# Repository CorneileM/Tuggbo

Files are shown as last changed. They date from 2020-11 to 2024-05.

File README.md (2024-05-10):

# Tuggbo
## Type: Robot/Thingy
### An automated filament pulling device to control 3D-printer filament diameter when exiting a filament extruder

This repository contains circuit diagrams, 3D-printed parts, and Arduino sketches for a filament pulling device designed to control the diameter of 3D-printer filament exiting a desktop extruder (in this case, a Filabot EX2).

The diameter of the filament is controlled by the speed of a DC motor which pulls filament from an extruder:
faster pulling = thinner filament; slower pulling = thicker filament. The filament is air- or water-cooled before it reaches the filament pulling machine. The speed of the DC motor is adjusted based on the measured filament diameter
which is read from a Mitutoyo digital plunge-dial indicator, to obtain a stable filament diameter. Because there's a lag period between filament exiting the extruder and being measured and an additional lag period between Tuggbo pulling speed adjustments and filament diameter change, I implemented a PID controller algorithm to obtain a stable filament diameter. 

The repository also includes an Arduino sketch and circuit diagram for a PID controlled heater that is placed inside the FILABOT EX2 hopper, to pre-heat and soften plastic pellets 
before entering the extrusion screw. This functions to prevent the the extrusion screw from being blocked by large pieces of hard plastic. This is specific to my application of producing filament from recycled plastic bottles. Preheating allowed for smoother plastic flow from the hopper into the extruder screw.

<br>

#### Tuggbo

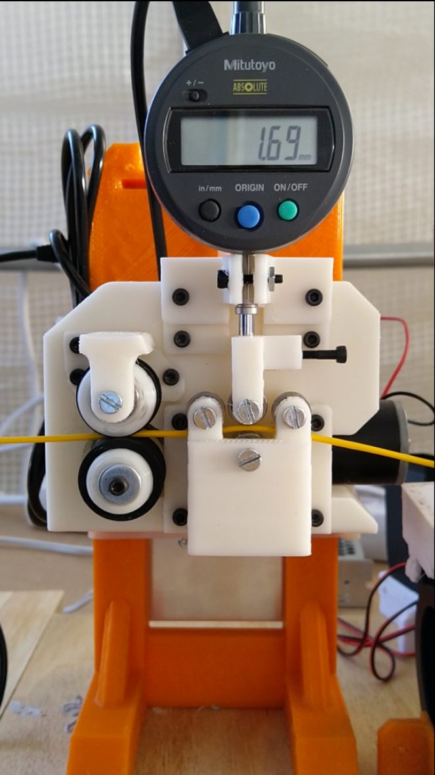
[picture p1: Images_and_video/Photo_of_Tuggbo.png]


<br>

### Useful resources and background information
#### PID process control
[Interfacing a digital micrometer and a microcontroller]( https://www.instructables.com/id/Interfacing-a-Digital-Micrometer-to-a-Microcontrol/ )

[Arduino PID library](https://playground.arduino.cc/Code/PIDLibrary/)

[PID explained for process engineers](https://www.aiche.org/resources/publications/cep/2016/february/pid-explained-process-engineers-part-2-tuning-coefficients)

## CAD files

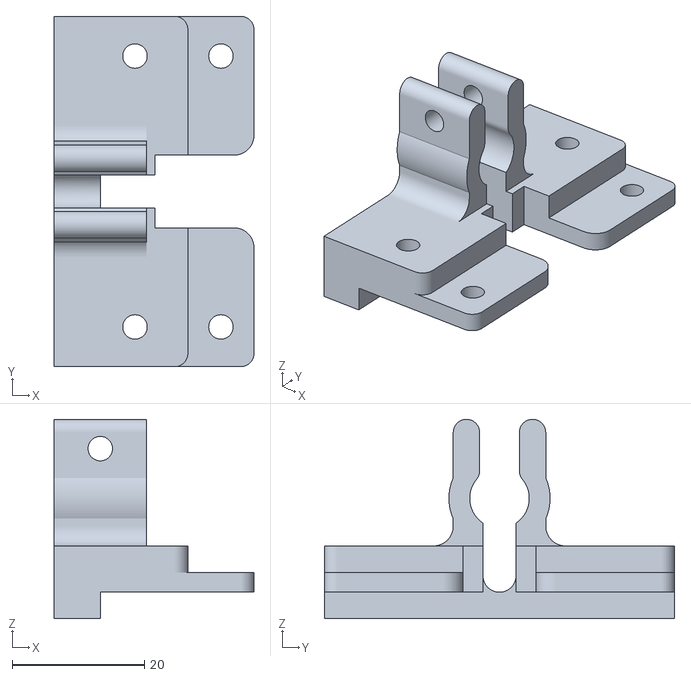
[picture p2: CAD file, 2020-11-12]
Tuggbo_3D_printed_parts/STLs/MituBaseClamp.stl
30.2 x 53.0 x 30.1

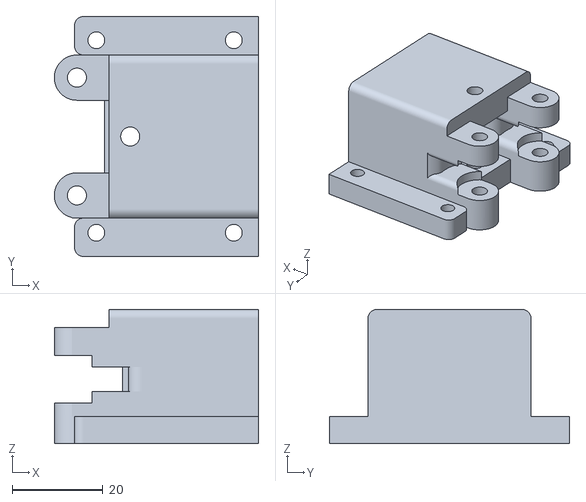
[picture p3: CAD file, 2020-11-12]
Tuggbo_3D_printed_parts/STLs/MituGhousing.stl
45.1 x 53.0 x 29.6

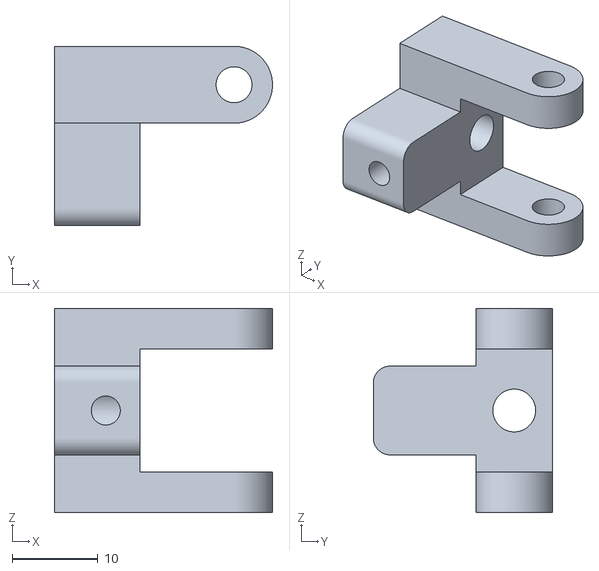
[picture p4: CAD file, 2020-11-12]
Tuggbo_3D_printed_parts/STLs/MituTip.stl
25.5 x 21.0 x 23.9

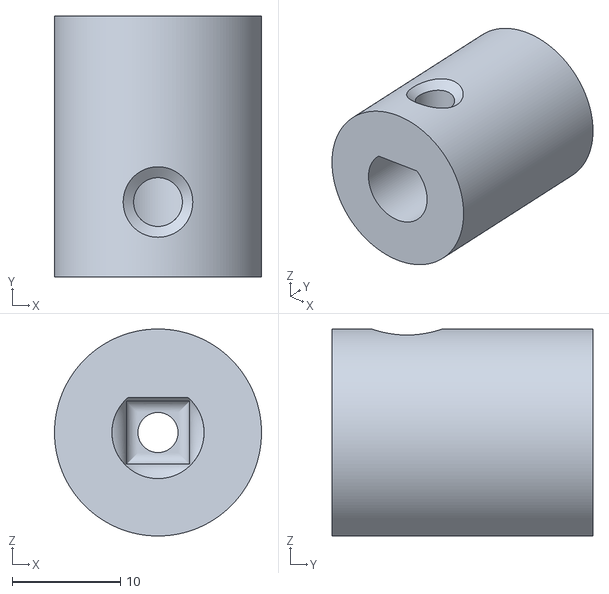
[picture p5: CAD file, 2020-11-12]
Tuggbo_3D_printed_parts/STLs/RWmotShaftIn.stl
19.1 x 24.0 x 19.1

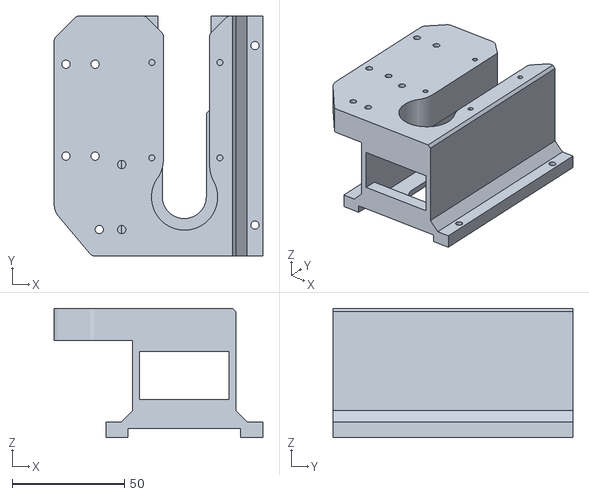
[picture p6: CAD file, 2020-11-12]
Tuggbo_3D_printed_parts/STLs/EngineCarriage.stl
93.0 x 107.0 x 57.6

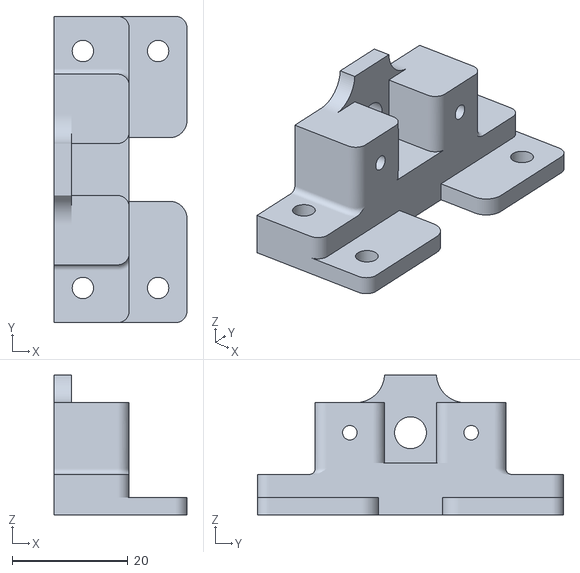
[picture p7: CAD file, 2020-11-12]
Tuggbo_3D_printed_parts/STLs/PullTensBase.stl
23.0 x 53.0 x 24.1

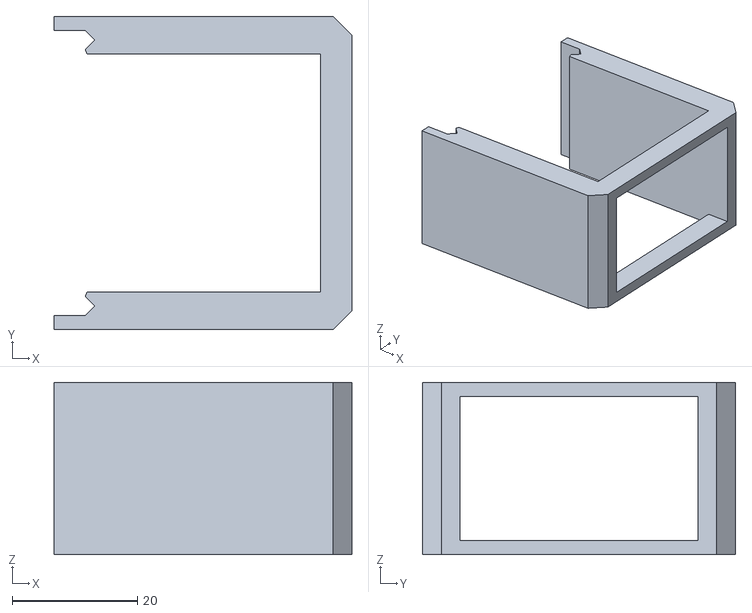
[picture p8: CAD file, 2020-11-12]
Tuggbo_3D_printed_parts/STLs/FanTop.stl
47.5 x 50.0 x 27.5

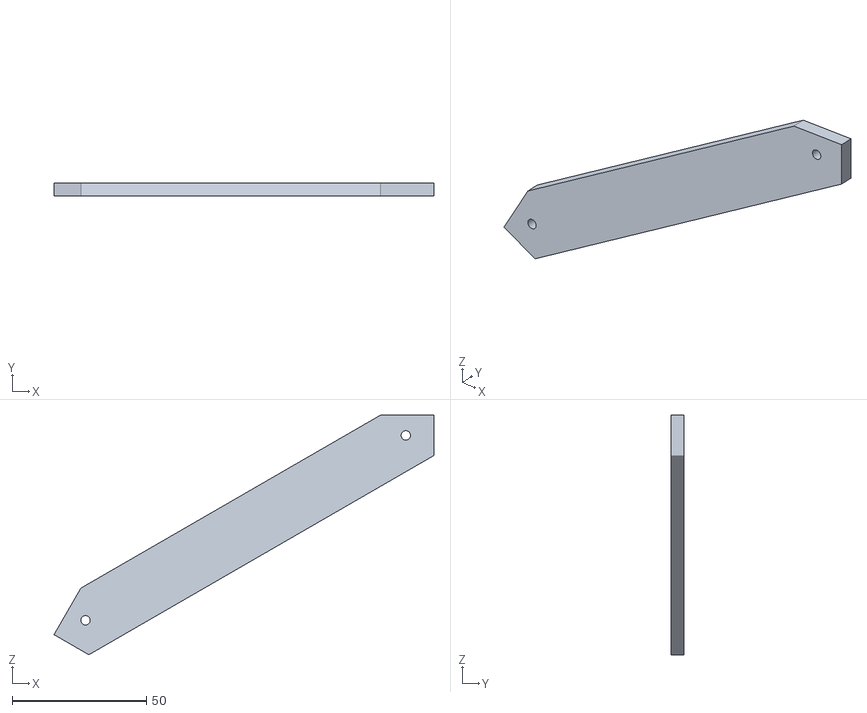
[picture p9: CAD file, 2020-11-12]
Tuggbo_3D_printed_parts/STLs/FanStruts.stl
141.6 x 5.00 x 89.3

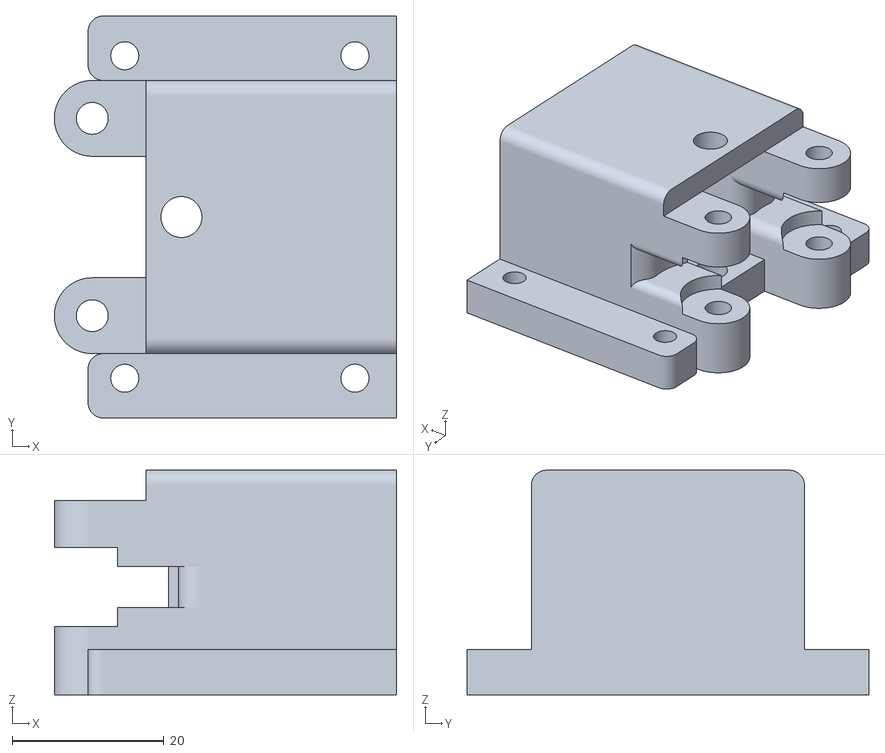
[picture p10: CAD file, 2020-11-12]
Tuggbo_3D_printed_parts/STLs/MotorGhousing.stl
45.1 x 53.0 x 29.6

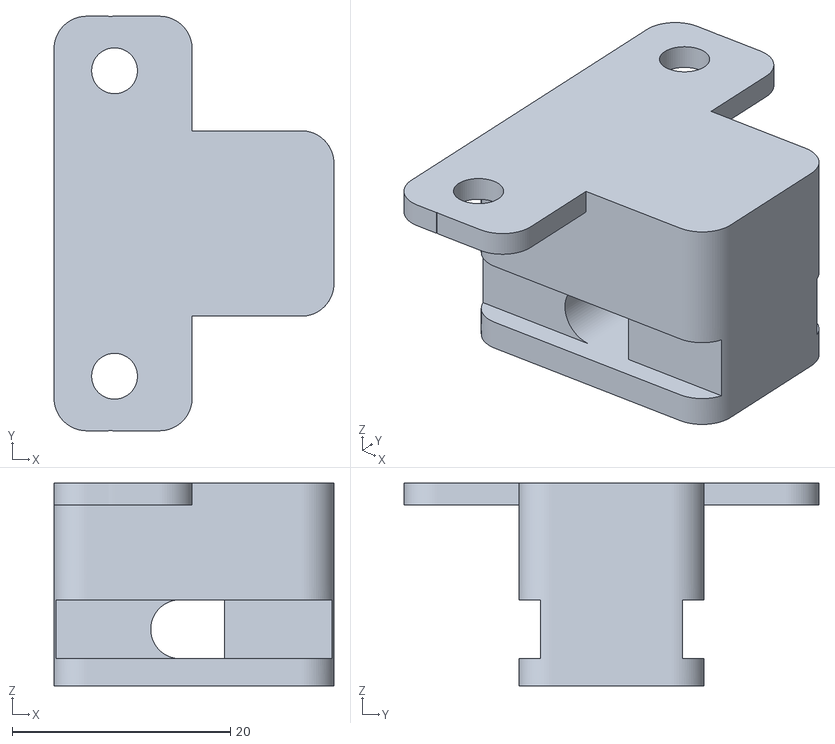
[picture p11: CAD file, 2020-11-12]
Tuggbo_3D_printed_parts/STLs/FillConduit.stl
25.7 x 38.0 x 18.6

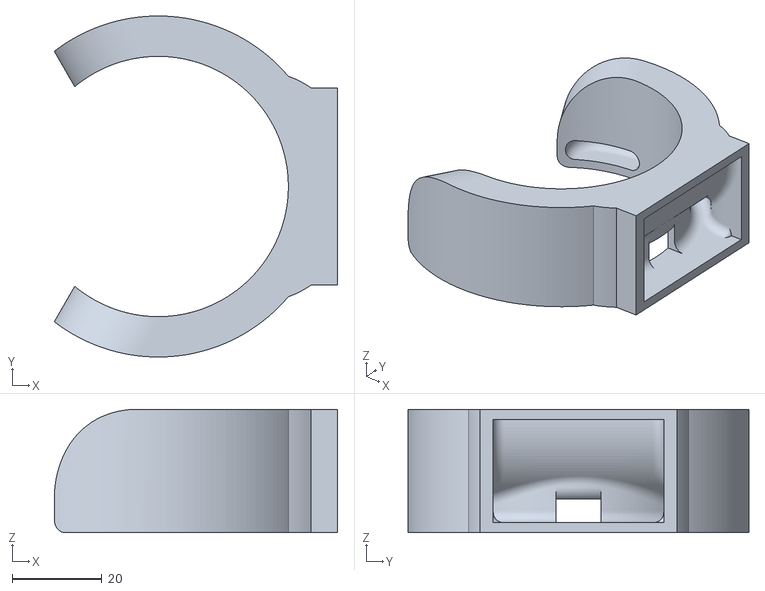
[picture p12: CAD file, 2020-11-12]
Tuggbo_3D_printed_parts/STLs/FanJets.stl
63.2 x 76.0 x 27.5

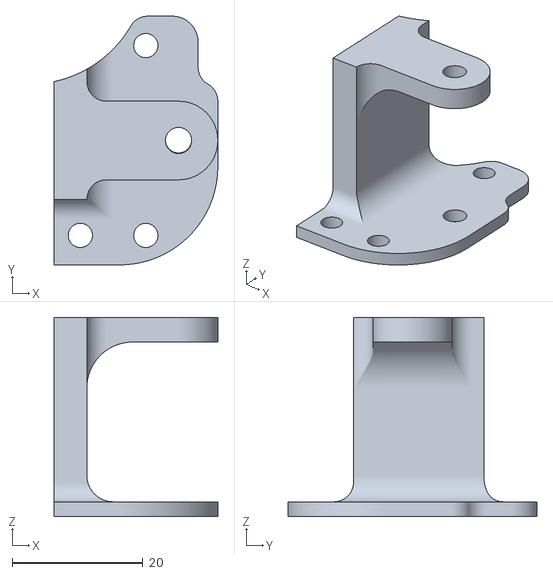
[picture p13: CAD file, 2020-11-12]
Tuggbo_3D_printed_parts/STLs/FreeWheelSupp.stl
25.0 x 38.0 x 30.4

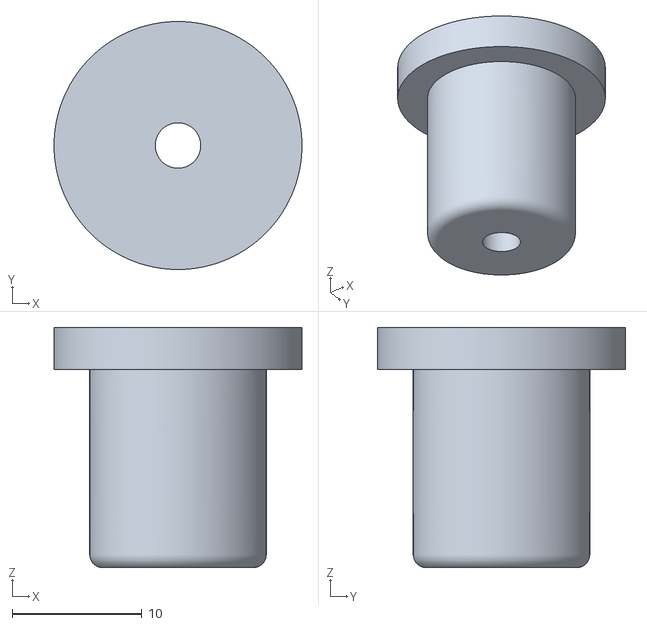
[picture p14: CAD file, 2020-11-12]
Tuggbo_3D_printed_parts/STLs/RWmotShaftOut.stl
19.1 x 19.1 x 18.5

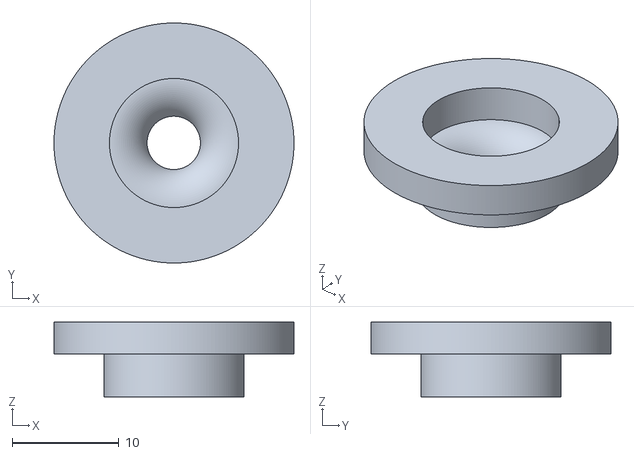
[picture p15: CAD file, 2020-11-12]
Tuggbo_3D_printed_parts/STLs/FreeWheelAxle.stl
22.5 x 22.5 x 7.00

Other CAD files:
Tuggbo_3D_printed_parts/STLs/PullTensPist.stl
Tuggbo_3D_printed_parts/STLs/FanBase.stl
Tuggbo_3D_printed_parts/STLs/FanBaseFilabot.stl

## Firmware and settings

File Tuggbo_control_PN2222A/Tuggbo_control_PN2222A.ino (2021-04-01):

//This sketch governs the behaviour of a filament pulling device designed to control the diameter of filament.
//The diameter of the filament is controlled by the speed of a DC motor which pulls filament from an extruder (Filabot EX2): faster = thinner filament; slower = thicker filament.
//The speed of the DC motor is adjusted based on the measured filament diameter which is read from a Mitutoyo digital plunge-dial indicator, to obtain a stable filament diameter.

//This sketch incoporates code from SSpence for reading data from the Mitutoyo plangue dial: https://www.instructables.com/id/Interfacing-a-Digital-Micrometer-to-a-Microcontrol/ 

  
//**LIBRARIES**//
#include <PID_v1.h>
#include <MovingAverage.h>

//**PIN AND VARIABLE DECLARATIONS**//

  //*MITUTOYO*//
    const int req = 5; //Mitutoyo REQ line goes to pin 5 through q1 (arduino high pulls request line low)
    const int dat = 2; //Mitutoyo Data line goes to pin 2
    const int clk = 3; //Mitutoyo Clock line goes to pin 3


   //Mitutoyo data variables//
    int i = 0;
    int j = 0;
    int k = 0;
    float MITread_x;
    float MITreadPush;
    float MITreadAve;
    float MITreadAveDiff;
    //const float MIToffset = 30; //Tuggbo#1
    //const float MIToffset = 20; //Tuggbo#2
    const float MIToffset = 15; //Tuggbo#3
                              //Because of a slight groove in the Mitutoyo's filament guide bearing, there is a 0.3 mm offset -- we multiply the offset by 100 to correspond with the raw data from the Mitutoyo
                              //The offset is currently subtracted manually and directly from setpoint and measured values, but will be implemented automatically at a later stage to give more intuitive outputs
    const float FilamentDiam = 1.65; //Sets the filament diameter goal we want. Units are mm/100. At the moment we're aiming for 1.35 mm filament
                                  //this seems to be the best diameter to achieve sufficient cooling with the current setup.

    float TargetHIGH = FilamentDiam+0.16;
    float TargetLOW = FilamentDiam-0.16;
    
    byte mydata[14];
    String value_str;
    long value_int;
    float value;
  
  //*MOSFET MOTOR CONTROLLER*//
    const int MOSFET = 6; //MOSFET PID (PWM) output goes through pin 6 -- this needs to be a PWN pin. On the Nano Every that's D3, D5, D6, D9, D10
    int pwmStart = 70; //variable determining motor speed
                       //stable at 55 

  //*PID FILAMENT DIAMETER CONTROL*//
    //define PID Variables
    double Setpoint, Input, Output;
    float Kp = 2; //The proportional gain (Kp) determines the ratio of output response to the error signal. In general, increasing the proportional gain will increase the speed of the control system response
                  //I'm setting this to 0.3, since preliminary tests showed that Tuggbo was reacting too quickly, even at Kp = 2
                  //0.5
                  
    float Ki = 0.75; //The integral component sums the error term over time. The result is that even a small error term will cause the integral component to increase slowly.
                    //The integral response will continually increase over time unless the error is zero, so the effect is to drive the Steady-State error to zero.
                    //0.15
                    
    float Kd = 0.25; //The derivative component causes the output to decrease if the process variable is increasing rapidly (in our case, this is reversed).
                  //The derivative response is proportional to the rate of change of the process variable.
                  //Increasing the derivative time (Td) parameter will cause the control system to react more strongly to changes in the error term and will increase the speed of the overall control system response.
                  //Most practical control systems use very small derivative time (Td), because the Derivative Response is highly sensitive to noise in the process variable signal.
                  //0.2
    
    //Specify the links and initial tuning parameters
    PID tuggboPID(&Input, &Output, &Setpoint, Kp, Ki, Kd, P_ON_E, REVERSE); //PID coefficients were taken from http://electronoobs.com/eng_arduino_tut24_2.php as a starting poinoinoi
                                                                      //I used to have the PID run on P_ON_M mode (proportional on measurement), but this seemed to make the PID very "scared" of going too close to the setpoint
                                                                      //Overshoot is not a big deal in this application, so I've switched this back to the standard proportional on error mode (P_ON_E)
                                                                      //We specify REVERSE, since the thicker the filament gets, the higher the output needs to be
  
  //*MOVING AVERAGE VARIABLES*//
    //Sets up the movingAverage function with 50 readings (1 per millisecond) per moving average window with a starting value of 0
    //This function will constantly calcualte a moving average for smoothed Mitutoyo readings -- the moving average window also serves to moderate Tuggbo's control response to make it less jerky 
    MovingAverage<float> MITread(5, 0);

    // Generates the first input for the MovingAverage function
    //float MITread_x = FilamentDiam*100;

    
void setup() {
  
  Serial.begin(9600); //Start serial communication

  //*MITUTOYO*//
    pinMode(req, OUTPUT); //Set the req (5) pin as an output so that data requests can be triggered by setting the pin LOW
    pinMode(clk, INPUT_PULLUP); //To obtain data we will read from the clk and dat pins, so they need to be set to INPUT with internal PULLUP resistors to stop noisy readings
    pinMode(dat, INPUT_PULLUP); //To obtain data we will read from the clk and dat pins, so they need to be set to INPUT with internal PULLUP resistors to stop noisy readings
    digitalWrite(req, LOW); // set initial state of req (5) pin to HIGH so that data can be requested from Mitutoyo by setting the pin LOW

  //*MOSFET MOTOR CONTROLLER*//
    //MOSFET pin is set to output so that we can send PWM signals to control the motor
    pinMode(MOSFET, OUTPUT); 

    //Define Input and Setpoint and turn the PID on
    Input = MITreadAve*100;
    Setpoint = FilamentDiam*100;
    tuggboPID.SetOutputLimits(pwmStart, 250); //since the motor only starts working at 43 PWM, we need to set the PWM min to 43. 70 is plenty fast, so I'm capping the max here.
    tuggboPID.SetMode(AUTOMATIC);

    //Starts the motor in forward direction at the motor starting speed
    analogWrite(MOSFET, pwmStart);
  
}

void loop() {

 //*MITUTOYO*//
   //get readings from the SPC cable (see https://www.instructables.com/id/Interfacing-a-Digital-Micrometer-to-a-Microcontrol/ for details)
  
    digitalWrite(req, HIGH); // request data from Mitutoyo

    for( i = 0; i < 13; i++ ) {
      k = 0;
      for (j = 0; j < 4; j++) {
        while( digitalRead(clk) == LOW) {
          } // hold until clock is high
          while( digitalRead(clk) == HIGH) {
            } // hold until clock is low
            bitWrite(k, j, (digitalRead(dat) & 0x1));
        }
        mydata[i] = k;
      }
    
    // assemble measurement from bytes    
    
    char buf[7];
    for(int lp=0;lp<6;lp++)
    buf[lp]=mydata[lp+5]+'0';
    buf[6]=0;
    MITread_x = atol(buf); //assembled measurement, no decimal place added
   
    digitalWrite(req, LOW); //reset req (5) pin to HIGH to stop data request
    
  //*MOVING AVERAGE CALCULATION*//
    // Pushes the MITUTOYO reading as an input to the moving average object
    /*if(MITread_x > 180){ // outliers sometimes pop up and cause shit... this eliminates false highs
      MITread_x = 180;
      
    }if(MITread_x < 60){ // outliers sometimes pop up and cause shit... this eliminates false lows
      MITread_x = 60;
    }*/

    MITreadPush = (MITread_x + MIToffset)/100;
    if(MITread.size() > 4){
      MITreadAveDiff = abs(MITreadPush - MITread.get());
      if(MITreadAveDiff > 0.25){
         delay(10);
         //get readings from the SPC cable (see https://www.instructables.com/id/Interfacing-a-Digital-Micrometer-to-a-Microcontrol/ for details)
  
            digitalWrite(req, HIGH); // request data from Mitutoyo
        
            for( i = 0; i < 13; i++ ) {
              k = 0;
              for (j = 0; j < 4; j++) {
                while( digitalRead(clk) == LOW) {
                  } // hold until clock is high
                  while( digitalRead(clk) == HIGH) {
                    } // hold until clock is low
                    bitWrite(k, j, (digitalRead(dat) & 0x1));
                }
                mydata[i] = k;
              }
            
            // assemble measurement from bytes    
            
            char buf[7];
            for(int lp=0;lp<6;lp++)
            buf[lp]=mydata[lp+5]+'0';
            buf[6]=0;
            MITread_x = atol(buf); //assembled measurement, no decimal place added
           
            digitalWrite(req, LOW); //reset req (5) pin to HIGH to stop data request

            MITreadPush = (MITread_x + MIToffset)/100;
            MITread.push(MITreadPush);
            
      } else {
        MITread.push(MITreadPush);
      }
    } else {
      MITread.push(MITreadPush);
    }

    // Prints each value stored in the moving average for debugging
    for (uint8_t i = 0; i < MITread.size(); i++) {
      Serial.print(MITread[i]);
      Serial.print(" ");
    }  

    MITreadAve = MITread.get();
    //Prints the moving average
    Serial.print(" = | ");
    Serial.print(MITread.get());
    Serial.print(" mm |");
    
    //*PID FILAMENT DIAMETER CONTROL*//
    //if there is no filament is present, we want the motor to continue turning at its minimum speed (0.2 mm is a safe margin for no filament being present)
    //if filament has been fed in (i.e., the Mitutoyo reads higher than 0.2) start PID motor control  
    if(MITreadAve < 1.00) { 
       Serial.print("   THIN/NO FILAMENT: "); //for debugging purposes
       Serial.println(pwmStart); //for debugging purpose
       
       analogWrite(MOSFET, pwmStart); 
    } else {
      Input = MITreadAve*100;
      Setpoint = FilamentDiam*100;
      tuggboPID.Compute();
      analogWrite(MOSFET, Output);
      
      if(MITreadAve > TargetLOW && MITreadAve < TargetHIGH) { 
        Serial.print("   TARGET: "); //for debugging purposes
        Serial.println(Output); //for debugging purposes+
        }
        
      if(MITreadAve > TargetHIGH) {       
        Serial.print("   THICK: "); //for debugging purposes
        Serial.println(Output); //for debugging purposes
        }

      if(MITreadAve < TargetLOW) {
        Serial.print("   THIN: "); //for debugging purposes
        Serial.println(Output); //for debugging purposes
      }
    }
    
delay(200);

}

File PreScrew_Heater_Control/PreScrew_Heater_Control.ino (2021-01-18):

// This Arduino sketch reads the voltage across a NTC (negative-temperature coefficient) thermistor, converts it to a temperature reading
// and switches a MOSFET connected to a heater cartridge on and of through a PWM signal to keep the temperature close to a set point which is controlled by a rotary encoder.
// Both the set point temperature and actual temperature are displayed on a LCD screen

//**CODE SOURCES**//
// Thermistor reading code, including calibration coefficients for the thermistor were taken from a blog post by Joshua Hrisko: https://makersportal.com/blog/2019/1/15/arduino-thermistor-theory-calibration-and-experiment
// Rotary encoder interrupt code for Arduino Nano every adapted from forum discussion: https://forum.arduino.cc/index.php?topic=694732.0 

//**PIN OUTS**//

  /*ARDUINO -> LCD
   *A4 -> SDA
   *A5 -> SCL
   *5V -> LCD_5V
   *GND -> LCD_GND (make sure LCD ground is separate from the rest of the grounds)
   */
  
  /*ARDUINO -> ROTARY ENCODER
   *D2 -> A
   *D3 -> B
   *5V -> VCC
   *GND -> GND
   */
  
  /*ARDUINO -> THERMISTOR
   * A0 -> THERMISTOR LEAD 1 (one of the Thermistor leads, doesn't matter which one)
   * GND -> THERMISTOR LEAD 2 (one of the Thermistor leads, doesn't matter which one)
   * 3.3V -> Resistor (220K ohm) -> THERMISTOR LEAD 1 
   * There's also a 10uF capacitor connected between GND and 3.3V of the Arduino to reduce noise in the thermistor signal
   */
  
  /*ARDUINO -> MOSFET
   * 
   */

//**LIBRARIES**//
#include <Wire.h>
#include <LiquidCrystal_I2C.h>
#include <math.h>
#include <PID_v1.h>
#include <thermistor.h>

//**PIN AND VARIABLE DECLARATIONS**//

  //*LCD*//
    LiquidCrystal_I2C lcd(0x27,2,1,0,4,5,6,7);  // set the LCD address to 0x27 for a 16 chars and 2 line display

  //*ROTARY ENCODER*//
    static int pinA = 2; // Our first hardware interrupt pin is digital pin 2
    static int pinB = 3; // Our second hardware interrupt pin is digital pin 3
    volatile byte aFlag = 0; // let's us know when we're expecting a rising edge on pinA to signal that the encoder has arrived at a detent
    volatile byte bFlag = 0; // let's us know when we're expecting a rising edge on pinB to signal that the encoder has arrived at a detent (opposite direction to when aFlag is set)
    volatile int encoderPos = 30; //this variable stores our current value of encoder position. Change to int or uin16_t instead of byte if you want to record a larger range than 0-255
    volatile int oldEncPos = 0; //stores the last encoder position value so we can compare to the current reading and see if it has changed (so we know when to print to the serial monitor)
    volatile byte reading = 0; //somewhere to store the direct values we read from our interrupt pins before checking to see if we have moved a whole detent

  //*THERMISTOR*//
    thermistor therm1(A0,80);  // Analog Pin which is connected to the 3950 thermistor 100K connected to a 4k7 Pull up and 10Uf Capacitor. 80 represents the configuration in the library for this thermistor
    float T_conv;
    float THERMconvRead;

  //*PID TEMPERATURE CONTROL*//
    //define PID Variables
    double Setpoint, Input, Output;
  
    //Specify the links and initial tuning parameters
    PID heaterPID(&Input, &Output, &Setpoint,9.1,0.3,1.8,P_ON_M, DIRECT); //PID coefficients were taken from http://electronoobs.com/eng_arduino_tut24_2.php as a starting poinoinoi
                                                                      //P_ON_M specifies that Proportional on Measurement be used (see: http://brettbeauregard.com/blog/2017/06/introducing-proportional-on-measurement/)
                                                                      //We also specify DIRECT, since the hotter the cartridge gets, the lower the output needs to be
                                                                      
  //*MOSFET heater switch*//
    const int MOSFET = 6; //MOSFET PID (PWM) output goes through pin 6 -- this needs to be a PWN pin. On the Nano Every that's D3, D5, D6, D9, D10

  //*TIMING VARIABLES*//
    //We'll use millis as a timer to loop through multiple samplings of the thermistor, and a samplecounter to set and keep track of the number of samples taken before averaging the reads
    unsigned long previousMillis = 0; //set to zero to begin
    const int intervalMillis = 100; //sets the sampling interval that we want -- let's set the interval to 0.2 seconds for now
    unsigned int sampleCount = 0; //placeholder to count the number of sample readings taken from the Thermistor
    const byte sampleNum = 10; //sets the number of samples we want to take before averaging-- let's set this to 10 for now, which gives us an average reading over 2 seconds
    unsigned int THERMreadTotal = 0; //placeholder to add each new reading to. This will be divided by sampleNum once sampleNum is reached to get an average

void setup() {

  //setup pins and interrupts for rotary encoder
  pinMode(pinA, INPUT_PULLUP); // set pinA as an input, pulled HIGH to the logic voltage (5V or 3.3V for most cases)
  pinMode(pinB, INPUT_PULLUP); // set pinB as an input, pulled HIGH to the logic voltage (5V or 3.3V for most cases)
  attachInterrupt(digitalPinToInterrupt(pinA), PinA, RISING); // set an interrupt on PinA, looking for a rising edge signal and executing the "PinA" Interrupt Service Routine (below)
  attachInterrupt(digitalPinToInterrupt(pinB), PinB, RISING); // set an interrupt on PinB, looking for a rising edge signal and executing the "PinB" Interrupt Service Routine (below)

  //initialize serial communication at 9600 bits per second:
  Serial.begin(9600);

  //Define Input and Setpoint and turn the PID on
  Input = T_conv;
  Setpoint = encoderPos;
  heaterPID.SetMode(AUTOMATIC);

  //set analog reference to read AREF pin
  analogReference(EXTERNAL);

  //setup LCD  
  lcd.begin(16,2); // initialize the lcd 
  lcd.setBacklightPin(3,POSITIVE);
  lcd.setBacklight(HIGH);
  lcd.clear();
  lcd.setCursor(0,0);  
  lcd.print("T:      Tset:"); // print prepeositions of temperature and Tset on LCD 
  lcd.setCursor(0,1);  
  lcd.print("Output:   "); // print prepeositions of temperature and Tset on LCD 

  // Display default Tset
  lcd.setCursor(13,0);
  lcd.print(encoderPos);   
    
}

//**ROTARY ENCODER INTERRUPT CODE**//
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

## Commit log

2020-11-12 Added 3D printed part STL files and gcode
    [EngineCarriage.stl, FanBase.stl, FanBaseFilabot.stl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]
2020-11-13 Changed description of motor controller to MOSFET motor controller
2020-11-17 Changed motor speed control to Proportional-Integral-Derivative (PID) control.
    The simple proportional control loop I wrote before was resulting in very choppy motor speed adjustments. I'm hoping that implementing PID motor speed control will smooth things out a bit.
2020-12-03 Put the PID control function inside of the averaging loop for filament diameter
    This presumably results in better syncing between the PID control function and filament measurements.
2020-12-03 Update Filament_puller_control.ino
    Removed averaging by interval, and replaced with a moving average calculation for MITUTOYO readings. This results in a smoother PID response.
    The derivative coefficient has also been reduced to prevent Tuggbo from responding to aggresively to sub-setpoint increases in filament diameter.
    Tests show that Tuggbo mostly only responds if filament diameter goes over setpoint, and only responds sub-setpoint if filament increases in diameter very rapidly.
    [Filament_puller_control.ino]
2020-12-10 Added a stirring device to the mouth of the hopper to prevent air pockets forming inside the gravity fed pellet mass
    [Hopper_control.ino]
2020-12-14 Several minor, but important, changes to PID coefficients
2021-01-01 Various changes to setpoints and PID control parameters. These changes were necesary after installing new, longer nozzles onto the filabots.
2021-01-18 Numerous changes to filament diameter and PID parameters
2024-05-10 Removed 3D-printed Tuggbo parts from git-tracked files
    [EngineCarriage.stl, FanBase.stl, FanBaseFilabot.stl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]
2024-05-10 Adjustment to gitignore parameters
    [EngineCarriage.stl, FanBase.stl, FanBaseFilabot.stl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]
